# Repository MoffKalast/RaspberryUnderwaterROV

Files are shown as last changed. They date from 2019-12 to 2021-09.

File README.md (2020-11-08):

## Underwater ROV powered by a Raspberry Pi



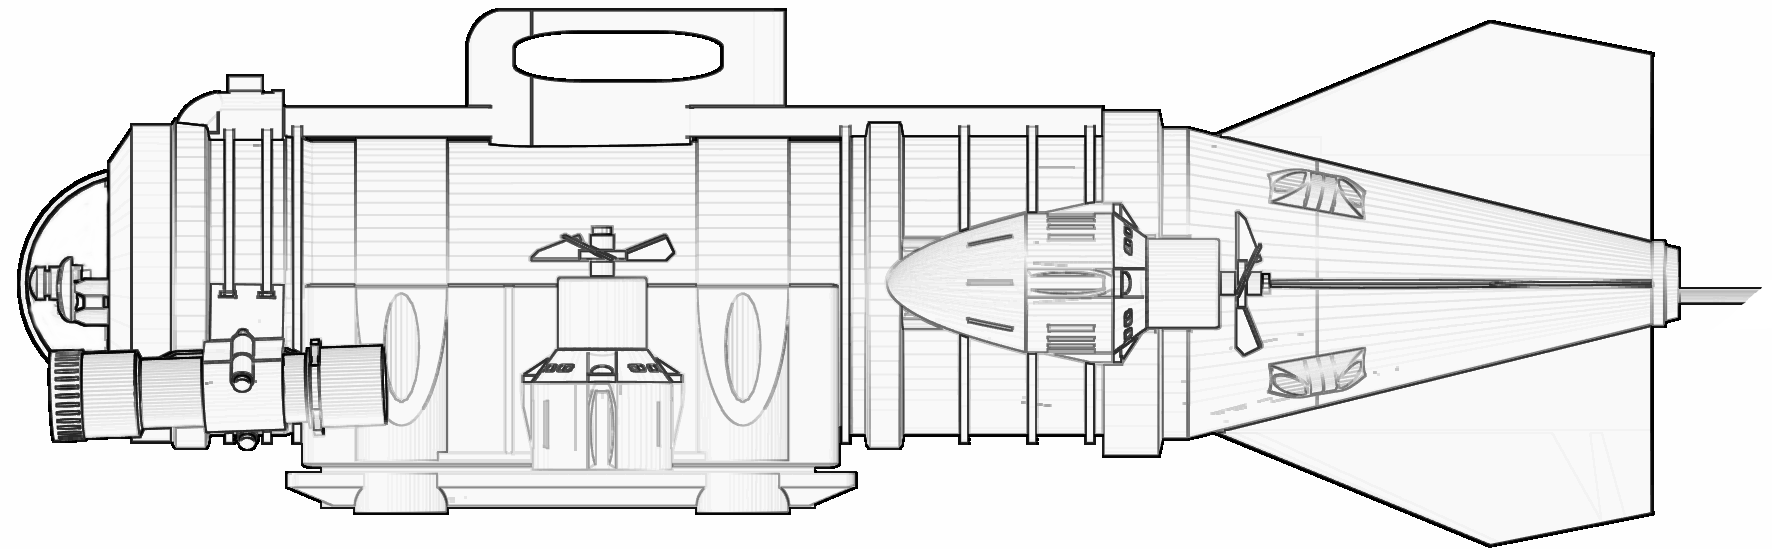
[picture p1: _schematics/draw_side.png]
Schematic


This codebase contains the control code for a homemade remotely controlled submarine and the Unity app for an android device that can be used to record video and drive the sub.

It uses a Raspberry Pi 2 as its central control unit, a Pi Camera V2 (later with D160 sensor) for custom video recording, sensors and drivers as described in the schematic below:

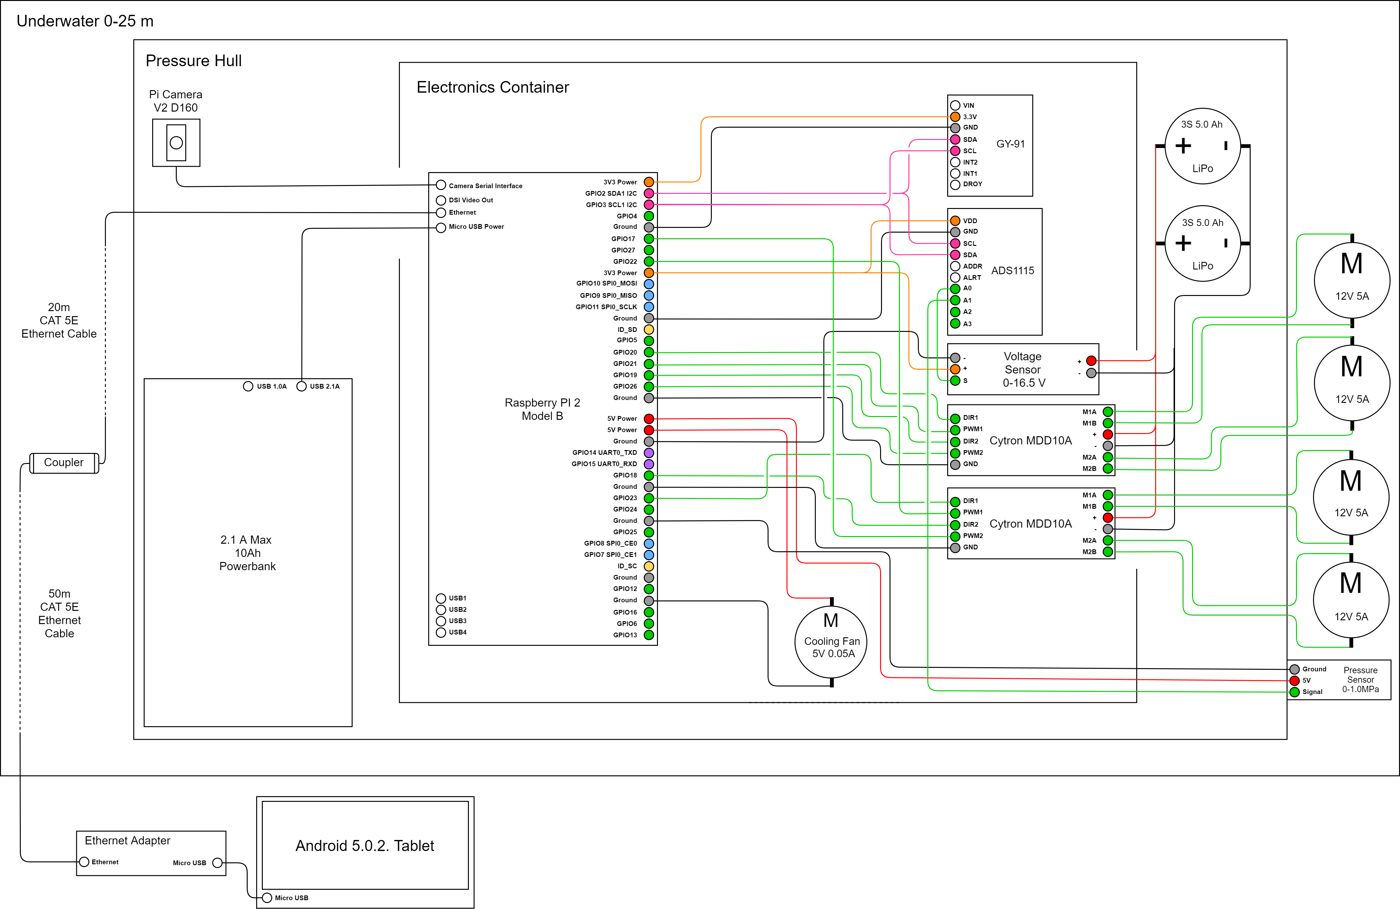
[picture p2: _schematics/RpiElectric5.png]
Electronics


The repository is divided into three parts:

- **/Submarine** which contains a NodeJS implementation of the submarine control software, along with video streaming and sensor AHRS, interfacting with the app using Socket.io

- **/ROVCommander** which is a Unity mobile app that allows for ease of control from a beach or boat

- **/ROViz** that contains the telemetry visualization application written in Godot (project source + exported Win64 binary)

See the subfolder README files for more information on each.

-------------

### Physical Implementation and Vehicle Tests

A test vehicle was constructed out of PVC-U sewer pipe with custom 3D printed PLA parts and an acrylic dome, all sealed together using epoxy glue.

Electronics

The following video contains a short summary of construction and testing.

IMAGE ALT TEXT HERE (https://www.youtube.com/watch?v=DufHhX7p4Xk)

All recorded uncompressed video during testing will be available for download if I ever find a place to host 50GB for free.

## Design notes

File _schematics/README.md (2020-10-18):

## Schematics

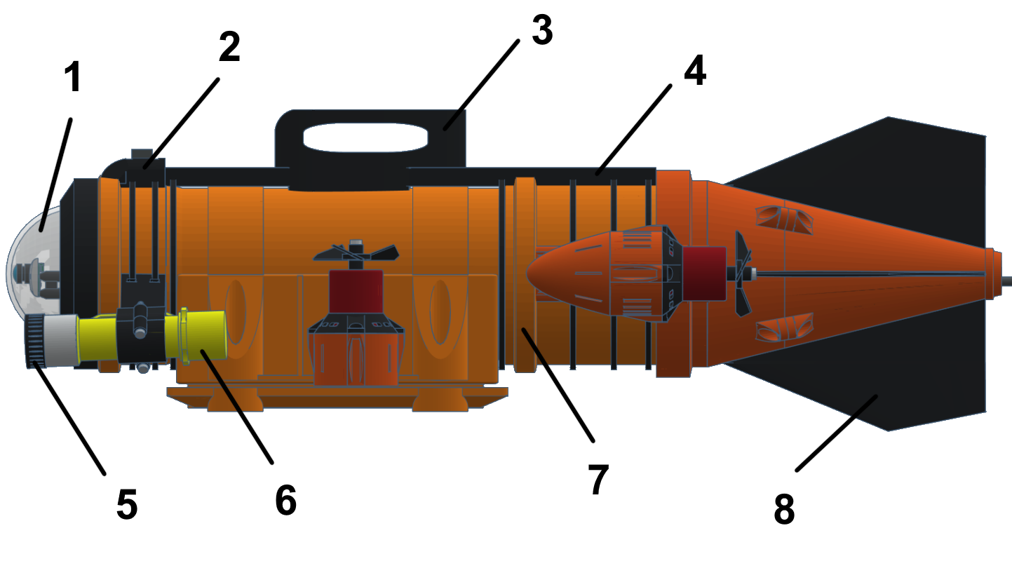
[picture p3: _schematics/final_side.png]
Schematic


1. Acrylic dome, 3mm thickness

2. GoPro mount

3. Sail/handle for stabilization and carrying

4. Sail rail

5. Light diffuser

6. Diving LED torches

7. Pressure hull (PVC sewer pipe)

8. Rear wings

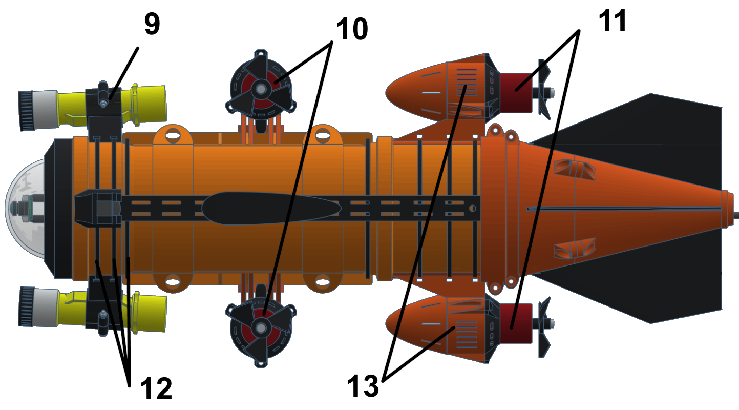
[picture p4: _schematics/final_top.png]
Schematic


9. Torch mount

10. Depth control thrusters

11. Planar motion thrusters

12. Zip ties

13. Engine nacelles

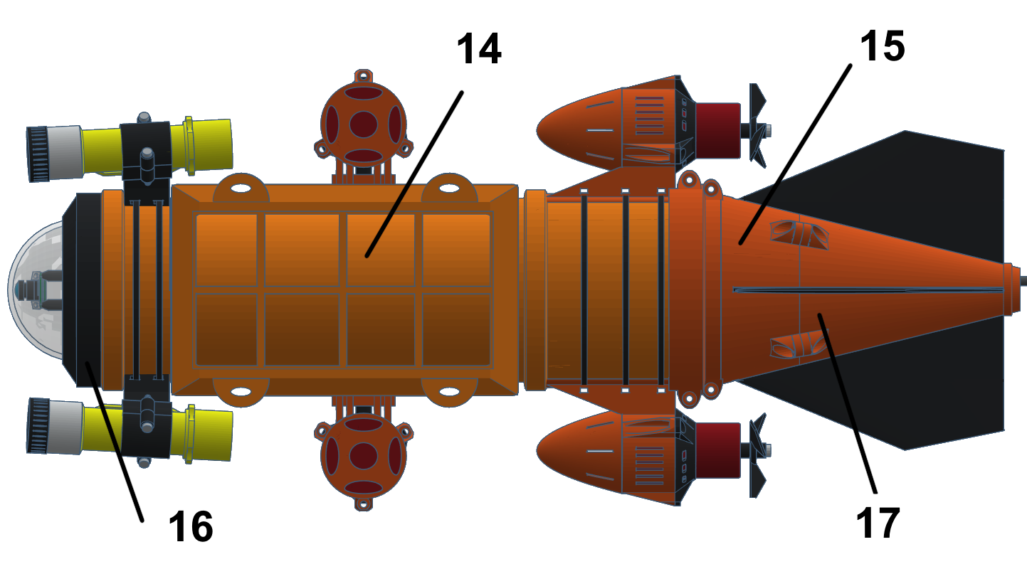
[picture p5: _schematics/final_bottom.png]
Schematic


14. Access hatch

15. Fixed tail assembly

16. Front shield

17. Detachable tail assembly

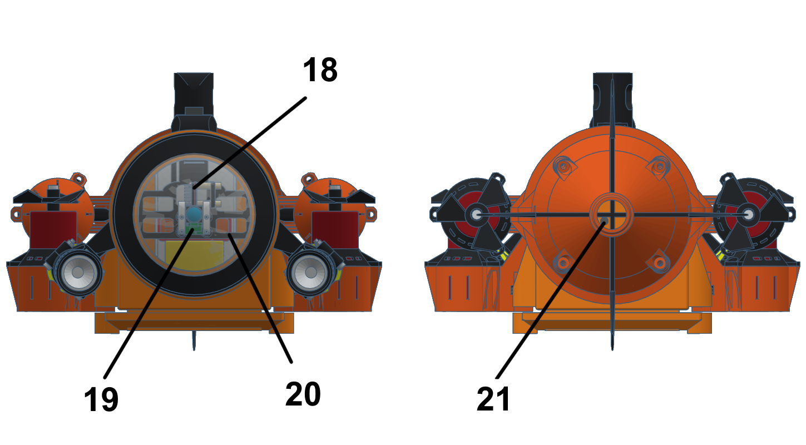
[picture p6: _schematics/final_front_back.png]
Schematic


18. IMU

19. Internal camera

20. IMU/camera mount

21. UTP cable

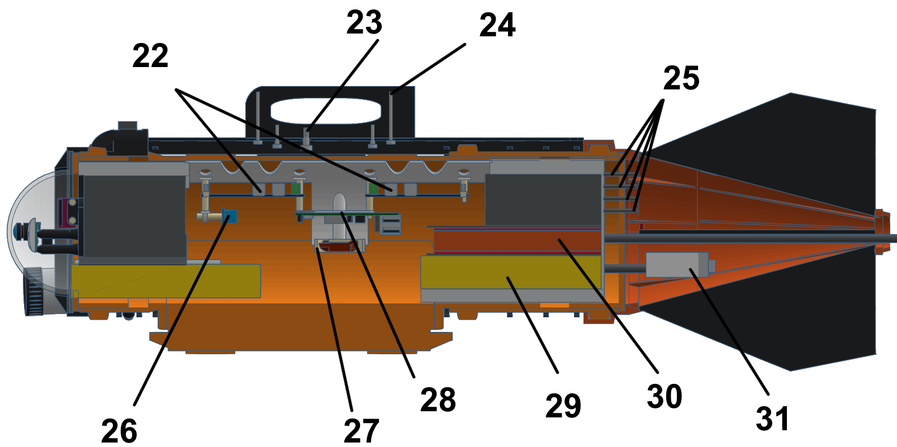
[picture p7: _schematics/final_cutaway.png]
Schematic


22. Motor drivers

23. M5 screw

24. M3 screw

25. Sealed motor wires

26. Voltage divider and ADC

27. 5V Fan

28. Raspberry Pi 2B

29. 5Ah 3S LiPo battery (motor supply)

30. 10Ah powerbank (Pi supply)

31. Water pressure sensor

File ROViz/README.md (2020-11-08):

### ROV Telemetry Visualizer - ROViz

A sort of RViz analogue app that visualizes recorded telemetry data in a 3D space using Godot 3.2.3.

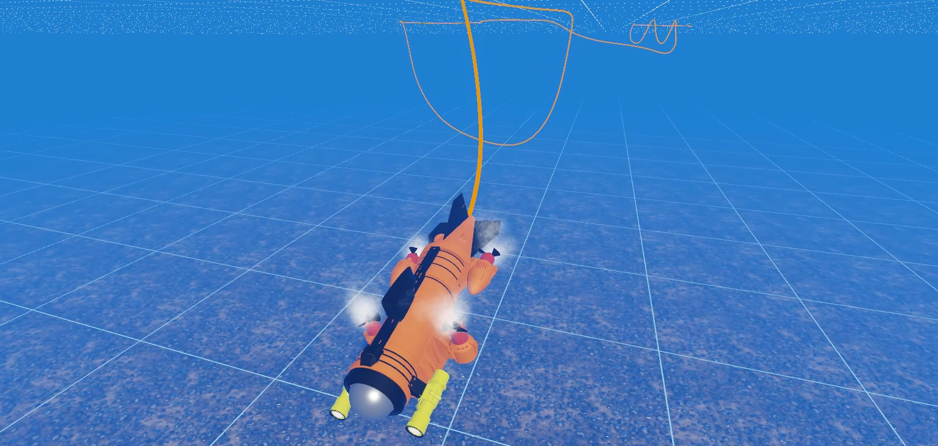
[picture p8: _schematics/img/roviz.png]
App


Features:
- 3D rendering of the submarine model with spinning propellers and particle effects
- raw value write out of currently displayed data
- timeline to track the data and a mark when the maximum depth was reached (after noise removal)
- file dialog to load telemetry files
- trail rendering to help track past movements

A curated collection of telemetry examples files can be found in the folder named as such.

Plugins used:

- [Godot-Trail-System](https://github.com/OBKF/Godot-Trail-System)
- [godot-realistic-water](https://github.com/godot-extended-libraries/godot-realistic-water/tree/master/realistic_water_shader)

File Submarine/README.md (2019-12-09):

## ROV Control Server

A NodejS implementation of a vehicle control software, mostly created to test out the absurd amount of Raspberry Pi hardware libraries for node on npm.

It enables differential drive control for two forward oriented thrusters, automatic heading and roll correction based on gyrocope data,  and depth hold based on pressure data and video streaming / recording using the Camera Module V2. Battery level is also approximated from voltage levels and battery type and forwarded to the control app along with internal hull air pressure, CPU temperature and air temperature.

When video recording is enabled a separate syncronized file of sensor data is also recorded and saved for later analysis.

Hardware Requirements:

- Raspberry Pi 2 B or later

- GY-91

- ADS1115

Software Requirements:

- Python 3

- NodeJS

- pigpio

Libraries used (all of these can be found by their name on NPM):

- data-store (storing settings, as all user inputed settings from the app are stored locally on the server, enabling quick switching of client devices in case one falls into water and dies)

- fs (sensor telemetry file writing)

- shelljs (enabling the app to run bash terminal commands on demand)

- python-shell (the node server runs a python script for video streaming since that seemed the only straightforward way to use the native python Raspicam library that enables usage of splitter ports)

- express, http, socket.io (communcation)

- pigpio (motor control)

- node-ads1x15 (reading the ADS1115 ADC for outside water pressure and battery level data)

- i2c (used for reading a LSM303 sensor that was later replaced by a GY-91)

- mpu9250 (9-dof sensor data readouts)

- bmp280-sensor (temperature and pressure readouts)

- ahrs (sensor fusion for 9-dof gyro/accelerometer/magnetometer sensor via a Mahony filter)

The modules are compiled for use on Raspbian Stretch and Raspberry Pi 2.

### Video Recording & Streaming

The software leverages the use of Raspicam splitter ports, allowing it to simultaneously stream/record video and save photos at different resolutions and formats.

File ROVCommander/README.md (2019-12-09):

### ROV Commander Unity App

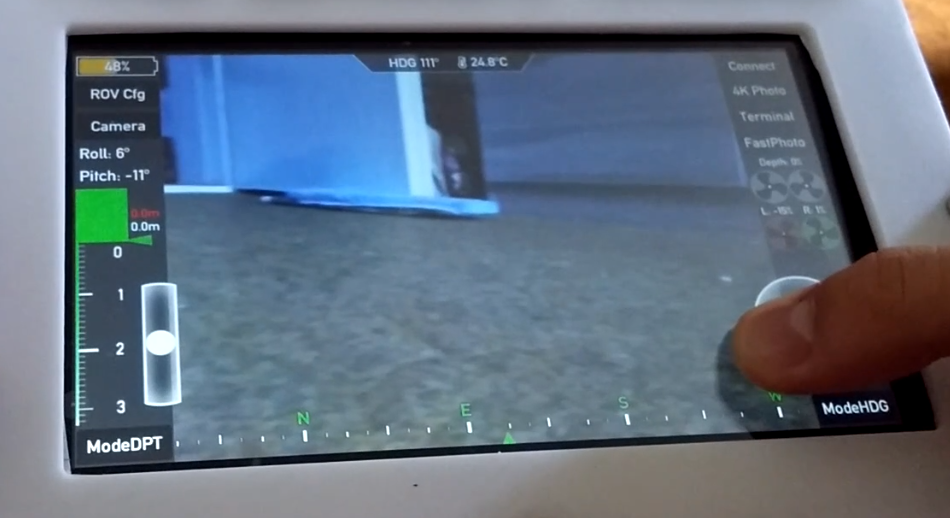
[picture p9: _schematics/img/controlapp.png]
App


Libraries used:

- [socket.io-unity](https://github.com/floatinghotpot/socket.io-unity)

- MjpegProcessor

The Unity project requires Unity 2017.4.26f1 due to the Socket.io library used for communication. The app presumes a LAN connection with the submarine control server, be it via an ethernet link + USB OTG or a wifi connection.

The app was developed exclusively for the Lenovo Tab 3, so minor gui tweaks may be needed for use on other devices.

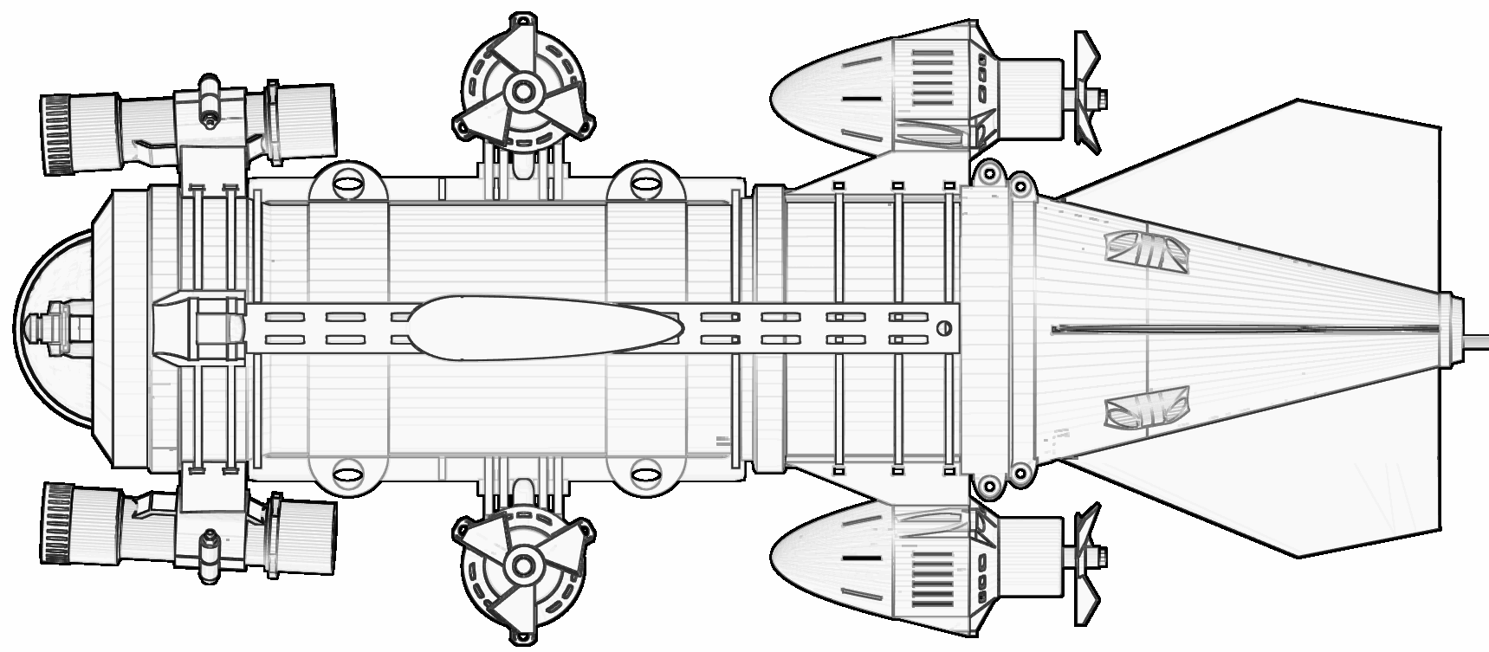
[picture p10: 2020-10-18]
_schematics/draw_top.png

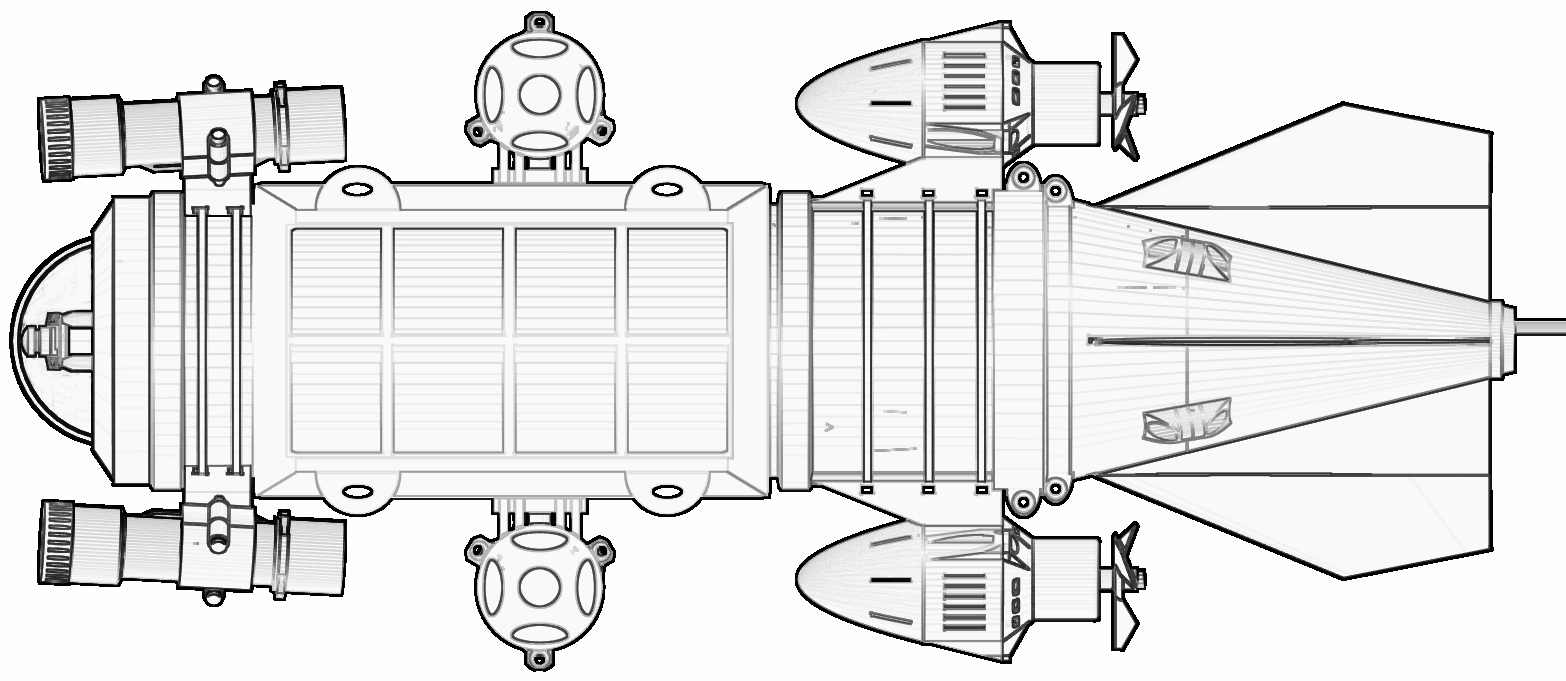
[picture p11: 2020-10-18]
_schematics/draw_bottom.png

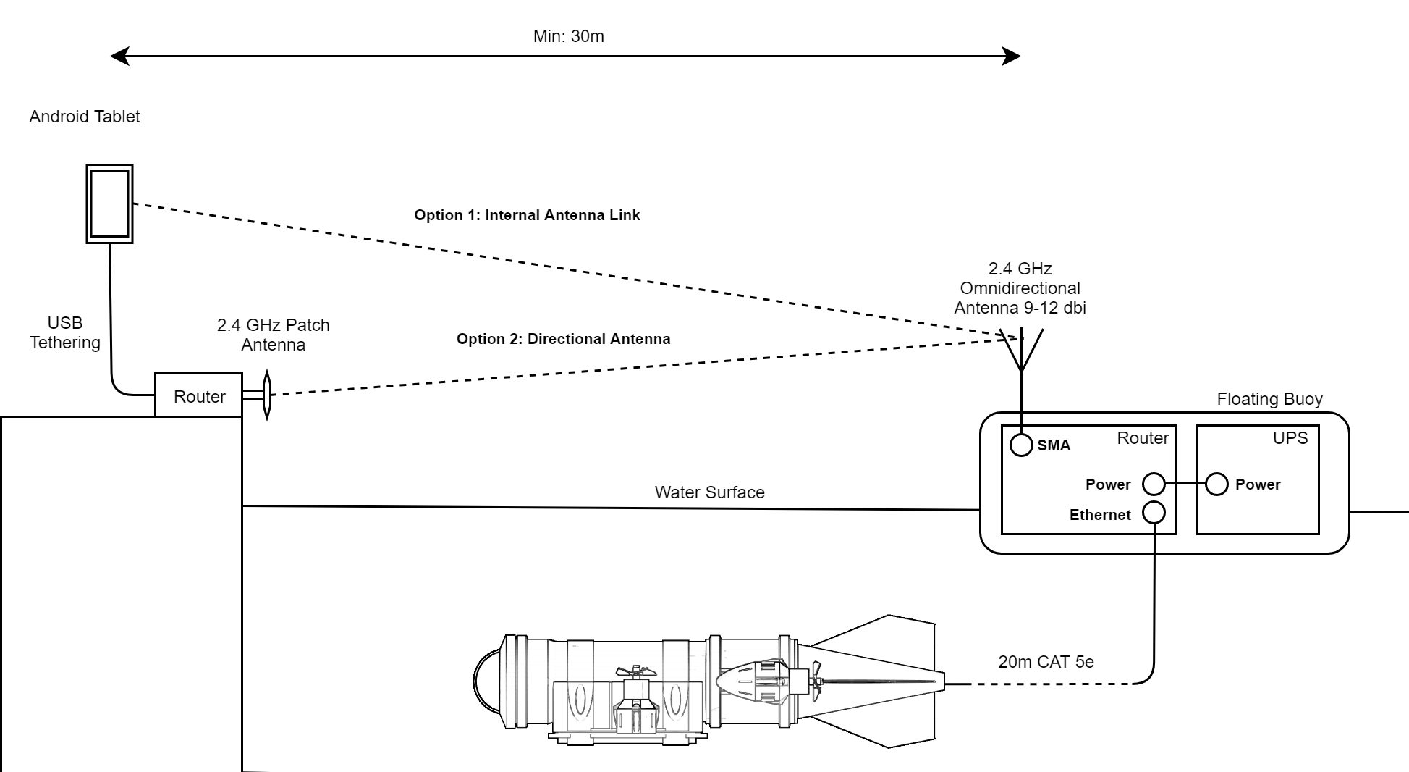
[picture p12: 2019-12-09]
_schematics/Link2.png

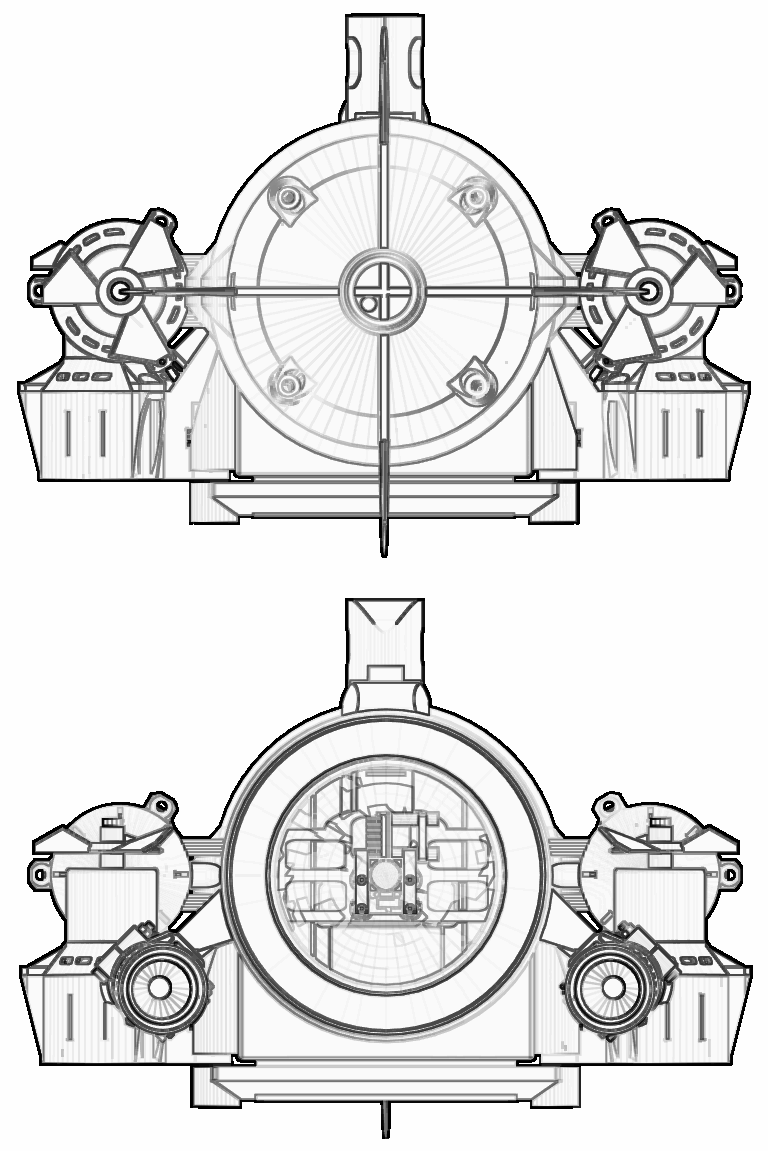
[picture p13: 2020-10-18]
_schematics/draw_front_back.png

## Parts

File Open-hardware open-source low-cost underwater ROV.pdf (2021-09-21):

# Open-hardware open-source low-cost underwater ROV

Vid Rijavec, Danijel Skocaj ˇ

University of Ljubljana, Faculty of Computer and Information Science E-mail: vid.rijavec@gmail.com, danijel.skocaj@fri.uni-lj.si

Abstract

As monitoring coastal regions becomes ever more topical due to unforeseen changes in ecosystems there still has not been a major breakthrough in marine robotics when it comes to mass accessibility. In this work we present our low-cost prototype of an underwater remotely operated vehicle (ROV) for coastal exploration and monitoring. We present the mechanical, electrical and software components of the developed ROV and describe the results of field tests. We made all the data, schematics, software, and documentation needed for construction of a such low-cost vessel publicly available.

Keywords

ROV, submarine, low-cost, Raspberry Pi

### 1 Introduction

Robotics has been making major strides in worldwide adoption, especially in unmanned ground and aerial vehicles (UGVs and UAVs) where prices have been dropping and with household robots entering mass production. The same cannot be said regarding autonomous underwater vehicles (AUVs) and remotely operated underwater vehicles (ROVs). The potential for such vessels includes controlling and monitoring large underwater areas without a large crew of divers and by users without diving certification. A number of species are already on the decline due to climate change [1], and those are being replaced by others, affecting ecosystems in unpredictable ways. As such, having access to more effective and low-cost AUVs and ROVs could help in detecting changes sooner, allowing for faster response and potential food chain collapse prevention. Similar applications involving monitoring coastal regions by utilising such an underwater robot are numerous.
There are many commercial options for buying a research ROV. High-end versions include the iBubble EVO [2] or the Blue Robotics BlueROV2 [3], with projects like the Blue Dot Model C [4] presenting a more affordable but less capable option. Given that even the low-cost options still aren’t truly affordable most enthusiasts still prefer to construct their own do-it-yourself (DIY) research vessel to customize it to their needs. However, most of these attempts tend to still be bulky and analog.

Our vessel, shown in Fig. 1, is designed as a combination of the classical AUV torpedo-like design and the typical boxy ROV designed for high movement accuracy, by combining the hydrodynamic hull shape with multiple control thrusters to allow for more degrees of freedom than a singular rear propeller. Our intention was to construct a fast-moving ROV that can explore a coastline from shore, one that’s controlled by a pilot using a tablet computer but offers advanced stabilization functions and an autopilot for ease of use. As such our design is a compromise between the two underwater vehicle types, giving the vessel greater speed at the cost of some maneuverability.

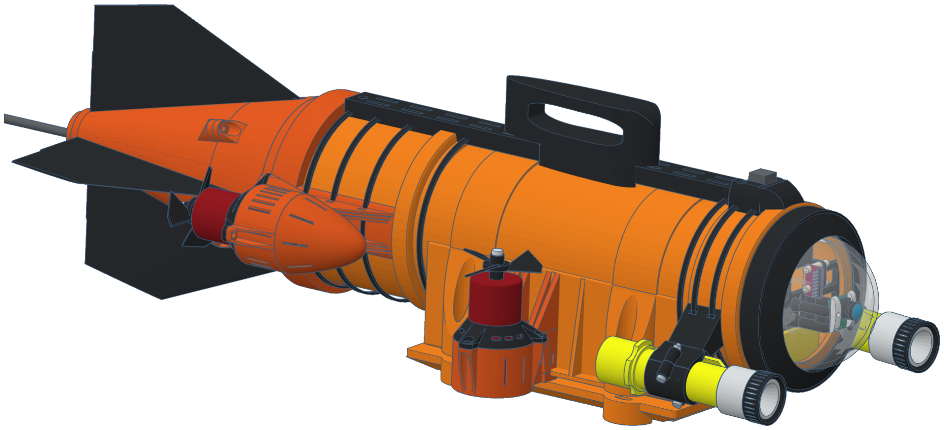
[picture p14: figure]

Figure 1: ROV CAD Model. The visible components of the vessel are: a PVC pressure hull, external LED lights, modified bilge pump thrusters (allowing movement in 4-DoF), rear stabilizers, a top handle, and a transparent camera dome.

The paper outlines the system and the specific components we’ve developed for it, with the rest of the code, schematics and documentation being available on Github [5].

### 2 Mechanical design

Figures 2, 3 and 4 present an overview of the ROV and its component parts, along with the tablet computer used by the pilot. The entire vessel is approximately 74 cm long and weighs just over 10 kg with batteries.
Building a sturdy and resistant pressure hull requires a rigid and non-permeable material that can be effectively glued to other parts. Out of all the tested low-cost components, the most cost-effective parts were determined to be PVC-U sewer pipe sections. We’ve used a cleaning section of pipe to make up the majority of the hull, as it has an external hatch which is practical for accessing internal electronics.
The front of the vessel is capped with an acrylic dome with a thickness of 3 mm, to allow the internal camera to see the underwater environment. It’s attached to the sewer pipe hull using epoxy glue and silicone caulking. The curvature of the dome later proved to be detrimental to the video quality as it added unwanted distortions and reflections. A more optimal design would involve the use of a thicker but flat (but smaller) front window. The video is then processed and sent over a length of rugged CAT 5E cable.

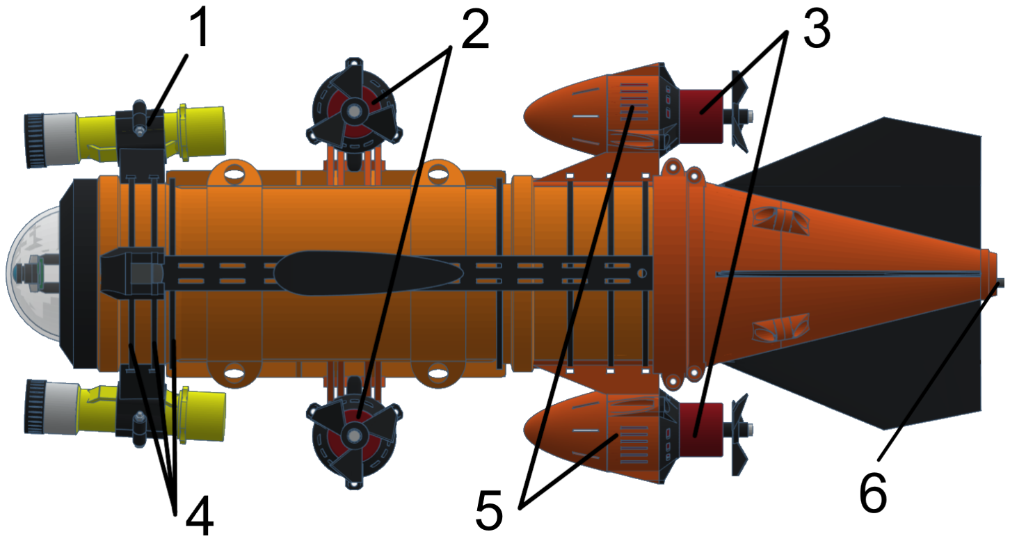
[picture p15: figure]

Figure 2: Top view of the vessel. 1. PLA flashlight mount. 2. Depth control thrusters. 3. Horizontal movement thrusters. 4. Zip ties. 5. PLA thruster nacelles. 6. CAT 5E cable.

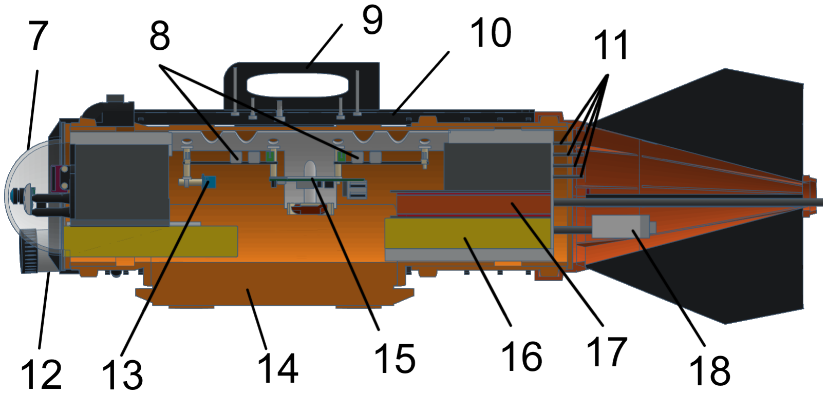
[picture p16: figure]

Figure 3: Internal cutaway of the vessel. 7. Transparent dome containing the Pi camera and IMU. 8. Cytron MDD10A motor drivers. 9. Dual purpose top fin and handle. 10. Steel structural rail. 11. Motor wires. 12. Diving flashlights with diffusers. 13. Voltage divider and ADC. 14. Access hatch. 15. Single board computer. 16. 2x 5 Ah 3S LiPo batteries. 17. 5 V 10 Ah Power bank. 18. Water pressure sensor.

Submersible DC bilge pump motors intended for clearing out any water that seeps into a ship’s bilge are a common choice for DIY ROV construction. The main appeals are the low cost, ease of modification and full water ingress protection. A simple improvement is to remove the pump’s impeller and housing, replacing them with a more efficient propeller [6] to achieve higher (and reversible) thrust. Our prototype uses nylon boat propellers sized at 56 mm. These motors do have a drawback -the o-ring seal around the shaft which exerts increasing amounts of drag with increasing pressure [7]. The seals fully block the shaft from rotating at around 25 m, which limits the sub’s operational depth. As such, using fully flooded brushless motors may be a better fit if greater depths are needed.
Rear wings aid with stabilization when moving at speed and were also chosen to be constructed out of PVC due to its light weight. The tail itself is not pressurized (typically called an outer or light hull which allows for water ingress) and houses the water pressure sensor, the tail fins, and protects the power/data cables along with providing better hydrodynamic performance.

### 3 Hardware and electronics

The electronics system as seen on the cutaway in Fig. 3 is centered around a single board computer, specifically the Raspberry Pi 2 Model B+, due to its low cost and lower TDP than later versions. The key features were GPIO pin access and the RJ45 socket which allows for an Ethernet link between the vessel and the control app on the surface. The surface component is a low-cost Lenovo tablet computer encased in a 3D printed housing that connects to the Ethernet link using an external USB dongle as seen in Fig. 4.

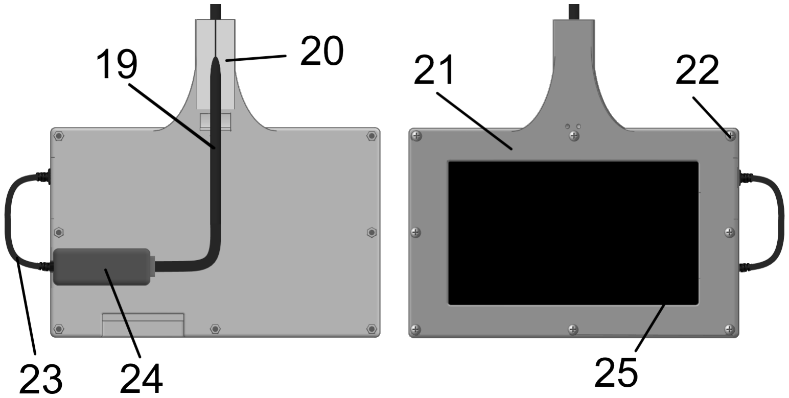
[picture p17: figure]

Figure 4: Tablet-based remote control system. 19. Reinforced CAT 5E cable (70 m total). 20. Cable clamp. 21. 3D printed splash-proof housing. 22. M3 screws. 23. Micro USB connector. 24. Ethernet network card. 25. Lenovo Tab 3.

### 3.1 Propulsion

As the ROV uses DC brushed motors (with a current rating of 5 A), we chose low cost Cyron MDD10A motor drivers to connect them to the Pi. Since the current rating of the drivers is twice the required maximum we can count on lower internal heating.

### 3.2 Sensors

The ROV is equipped with various sensors: an IMU, a water pressure (depth) sensor, a battery voltage sensor, an internal air pressure and a temperature sensor. We’ve also used a Pi Camera Module v2, and later the D160 fish eye modification for video recording.
We’ve used the MPU9250 IMU, which offers an accelerometer, gyroscope and magnetometer. The expansion board used is the GY-91 which also contains a BMP-280 pressure and temperature sensor, so that is used to log the state of internal air as well.
For the water pressure sensor we’ve selected a low-cost transducer intended for measuring the pressure inside hoses with a capability of 0.8 MPa (which equates to roughly 80 m depth of seawater). As the sensor is analog and the Pi has no analog reading pins we’ve also added a 10 bit 4-channel ADC to link the two together. As the ADC has spare channels we can also measure battery level using a voltage divider circuit.

### 4 Software

We’ve based our software around a socket.io link, which allows communication between the C# Unity app running on the remote control tablet, and the node.js server running on the submarine itself, which controls most of the functionality. To avoid having a rooted system on the tablet and a static IP, the Raspberry Pi instead acts as a DHCP server and assigns a known IP to any Ethernet connected device.
Not all of the system can be managed with node.js directly, as the libraries that allow full Pi Camera configuration have only been provided for Python and C++. Since the system requires the usage of GPU splitter ports to simultaneously stream and record video while taking pictures, the camera control part ended up being implemented in Python, which is then launched and managed from the node.js server.

### 4.1 Stabilization

We implemented two automatic functions: depth hold and heading hold. Establishing proportional control between the detected depth and target depth turned out to be enough to archive a satisfactory depth hold.
A more advanced system was required for holding a specific heading. An AHRS IMU fusion system [8] was added to get a good internal belief state regarding the submarine’s orientation. We’ve then implemented a 360-degree-capable proportional rotational system, which allows the pilot to input a single forwards or backwards speed while the vessel holds orientation.
Full PID controllers did not turn out to be required for adequate stabilization due to high drag and inherent damping and were also infeasible to properly tune during operation.
The system manages the aforementioned sensors and streams their data to the tablet, uses them internally for stabilization and also records them into a log file for later use.

### 4.2 Remote control app

We’ve implemented a front-end interface for controlling and configuring the submarine from a tablet computer, which was developed using Unity. The video arriving from the camera in a mjpeg format is displayed using an adapted version of the Mjpegprocessor library [9], while the rest of the telemetry and commands get routed through the socket.io library [10]. Fig. 5 shows the GUI while streaming the image of a calibration board, which indicates the camera field of view.
The main functionality is remote control, which is done either with manual joysticks or by selecting a direction using the bottom compass bar and a depth using a vertical depth indicator. In order to provide as much

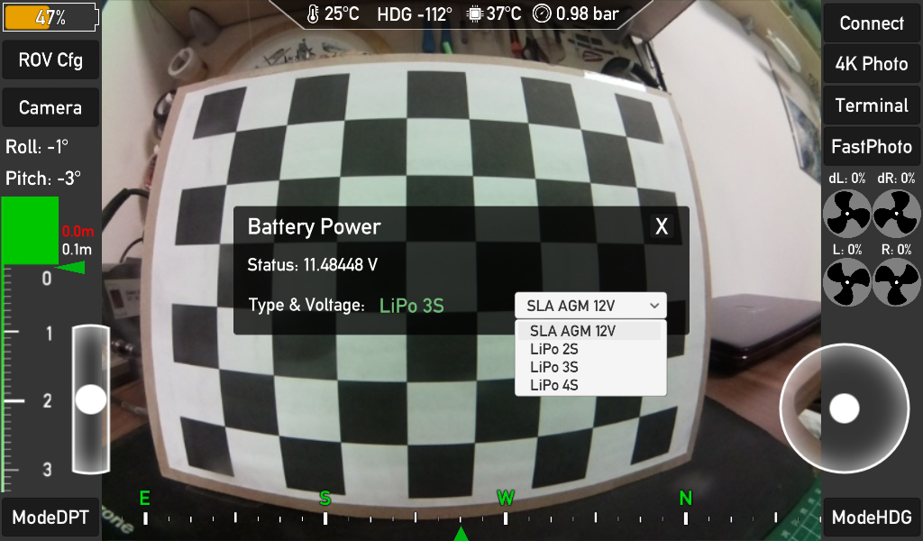
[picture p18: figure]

Figure 5: Layout of the tablet interface, showing the relevant telemetry and video feed.

on-site debugging power, the app can set all stabilization and video recording parameters and allow for rudimentary terminal access.

### 4.3 Visualization and analysis

We built a Godot engine visualizer to attempt to process the recorded log file data and reconstruct the ROV’s odometry to some degree as seen in Fig. 6.
The logged data gives us two absolute measurements: rotation (based on the fused IMU data) and depth (calculated from water pressure readings). It’s not possible to completely determine the movement path using just these two values, however, we also logged the individual thrusters’ speeds which were used to infer movement velocity. While it’s not possible to compensate for drift due to waves and currents the resulting movement path is still good enough in most cases.
While the data was logged every 100 ms, the visualization ran at a higher frequency (16 ms for 60 frames per second) so the data had to be linearly interpolated for smooth movement. A synced on-board video of a dive with the telemetry visualization which can be viewed on Youtube [11].

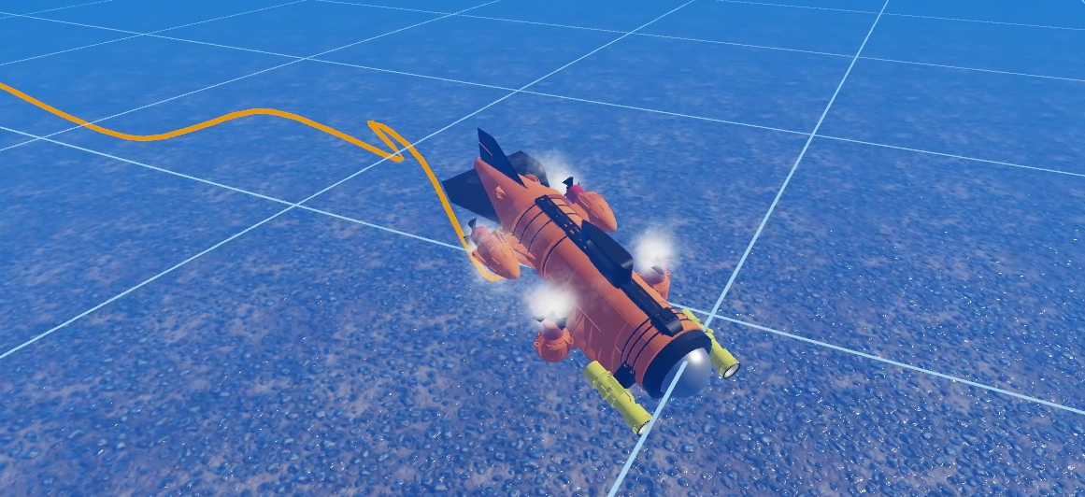
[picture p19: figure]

Figure 6: The ROV being rendered in Godot, visualizing a recorded dive and drawing a trail behind the vessel.

### 5 Evaluation and testing

The finalized ROV shown in Fig. 7 performed as required and is capable of exploring a coastal area while recording clear video as shown in Fig. 8. An edited compilation of video recordings that sums up research, construction and testing can be viewed on Youtube [12].

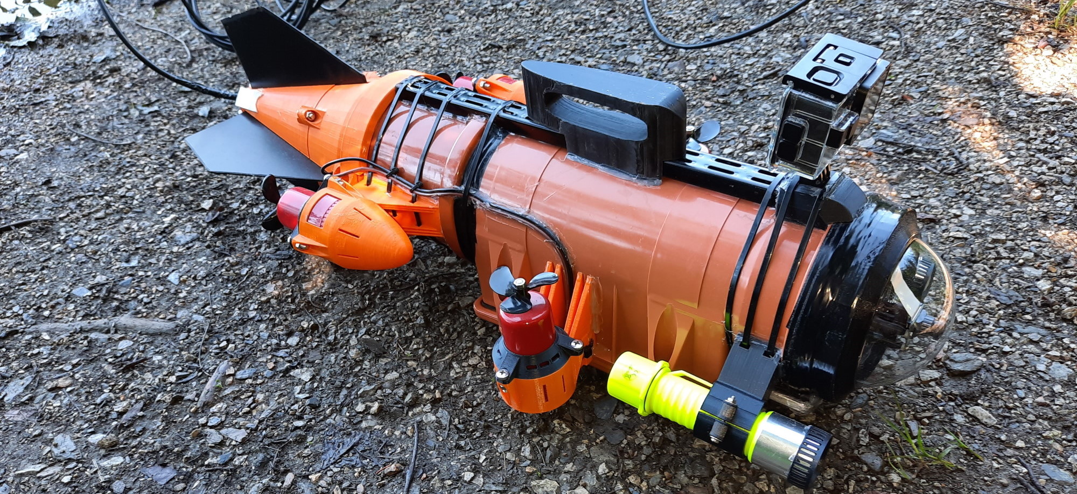
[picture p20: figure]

Figure 7: The ROV with an action camera mounted on the top rail.

To determine the effects of different buoyancy on the system’s operation, tests were done in both salt and fresh water. The difference ended up being minor, however, the depth calculation can be off by 2.5 % due to the extra mass of salt water. We therefore added parameters that can be changed in the mobile app to compensate for the changing environment.
We’ve used two different action cameras to record external video during testing: the Apeman A80 and later a GoPro Hero 9 Black combined with a red filter as the previous setup proved unsatisfactory. Having a red filter allows us to do an initial colour correction by restoring the lower wavelengths which get absorbed far more in water and lead to over-saturation of green and blue.
The recorded data shows that the air pressure in the ROV stays relatively constant regardless of depth, which would mean that there is minimal flex in the pressure hull as intended. The internal air temperature also stayed close to the external water temperature. It would appear the lack of isolation in the hull provides for excellent cooling and would allow for higher TDP computers to work without issues.

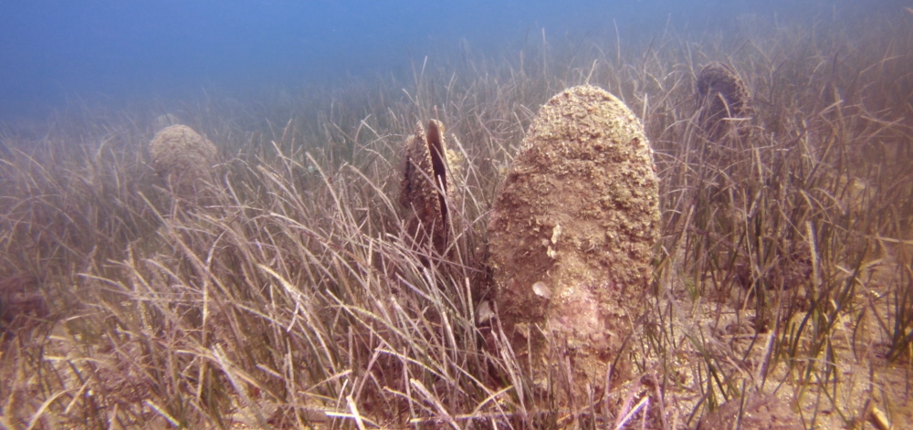
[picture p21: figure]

Figure 8: Fan mussles which were found in large numbers when testing in Izola, some of them decayed due to parasite infestation, confirming news sources [13].

Another addition to the system would be a sonar system for sea floor and obstacle detection, however, there are no affordable sensors that are capable of being integrated into a custom system at this time. One would need to construct a custom driver circuit for a commercial fish finder sonar transducer (e.g. TL88E, XF02), as conventional sonar sensors designed for AGV/AUV atmospheric usage lack the required power and do not operate in effective frequencies, which lowers the range and accuracy under water to unusable levels.

### 6 Conclusion

In this paper, we described the process of building a low-cost underwater DIY ROV with open-source hardware and software, useful for light research and monitoring of shallow coastal regions. We’ve achieved this goal by choosing a crush depth of 25 m and used less resistant and subsequently cheaper materials, as well as using 3D printed components to fill the gap between other parts. The total cost of the system ended up being around 400 C, excluding the tablet computer and action cameras.
The vessel is stable enough to record useful video due to the included IMU and sensor fusion, while being able to utilize its high top speed to rapidly traverse a chosen area and locate points of interest. The external mechanical design is robust enough to handle expected conditions, however the electrical internal setup could be further improved by designing a dedicated printed circuit board.

### 7 Acknowledgements

The authors would also like to thank professors Dr. Nikolaj Zimic and Dr. Matjaz Vidmar for their help and con- ˇ tributions in the research phase of the project.

References

[1] Marine Food Webs Are on the Brink of Collapse Because of Climate Change, https://futurism.com/marine-foodwebs-brink-collapse-because-climate-change
[2] iBubble - Your Personal Underwater Cameraman, http://ibubble.camera/product/ibubble-autonomousunderwater-drone
[3] Blue Robotics, http://bluerobotics.com
[4] Blue Dot Underwater Drones, https://www.bluedotrov.com
[5] Source code, schematics and documentation, https://github.com/MoffKalast/RaspberryUnderwaterROV
[6] Homebuilt ROVs - Seafox Retrofit Thrusters, https://www.homebuiltrovs.com/seafoxretrofitthrusters.html
[7] Homebuilt ROVs Mayfair 750 GPH Bilge Pump Thruster Testing,
http://www.homebuiltrovs.com/mayfair750test.html
[8] ahrs - npm, https://www.npmjs.com/package/ahrs
[9] SampleUnityMjpegViewer, https://github.com/DanielArnett/SampleUnityMjpegViewer
[10] socket.io-unity,
https://github.com/floatinghotpot/socket.io-unity
[11] ROViz visualization,
https://www.youtube.com/watch?v=M0sli2o5RJY
[12] Construction and testing video, https://www.youtube.com/watch?v=DufHhX7p4Xk
[13] Slovenian sea researchers uncover a number of deceased fan mussles, https://www.sta.si/2797119

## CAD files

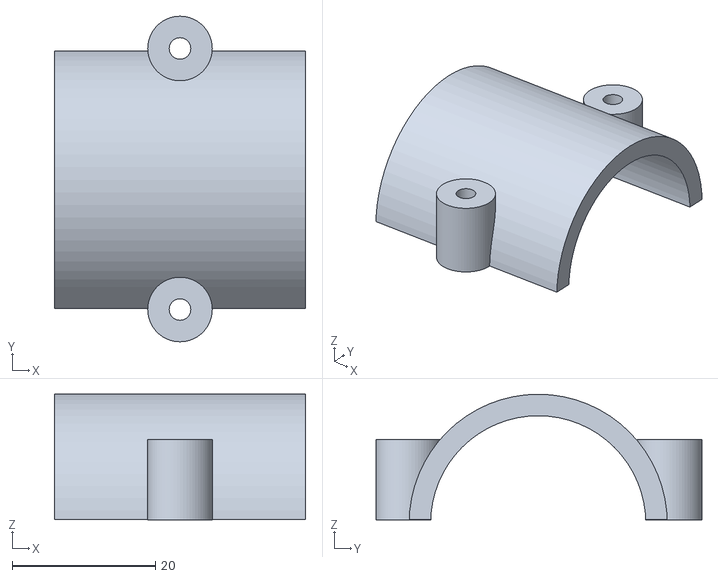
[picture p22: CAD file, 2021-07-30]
_schematics/cad/lamp_mount_clamp.stl
35.0 x 45.4 x 17.5

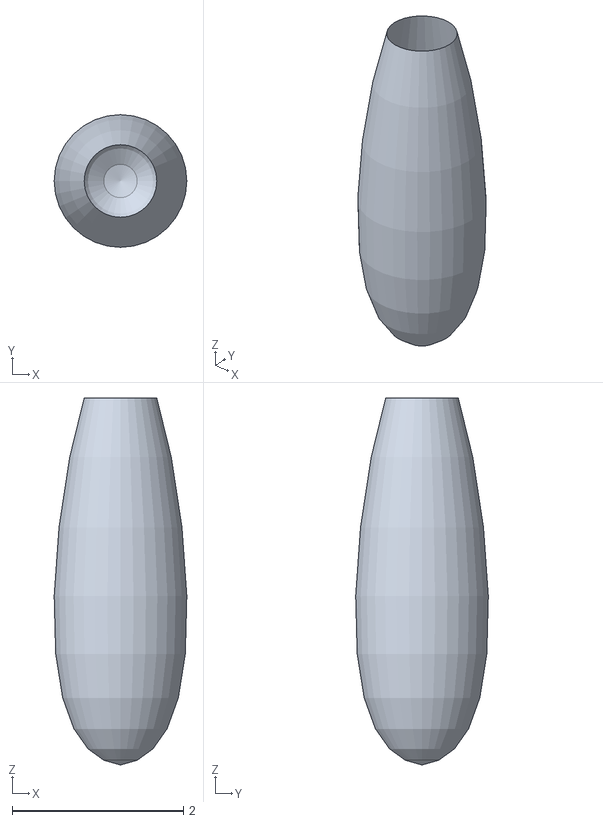
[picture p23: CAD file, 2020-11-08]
ROViz/source/assets/projectile_shape_1.obj
1.55 x 1.55 x 4.29

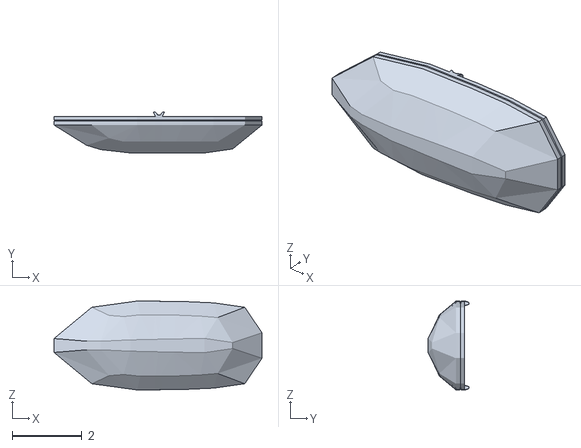
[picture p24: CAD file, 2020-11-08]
ROViz/source/realistic_water_shader/art/boat/Boat.obj
5.95 x 1.17 x 2.54

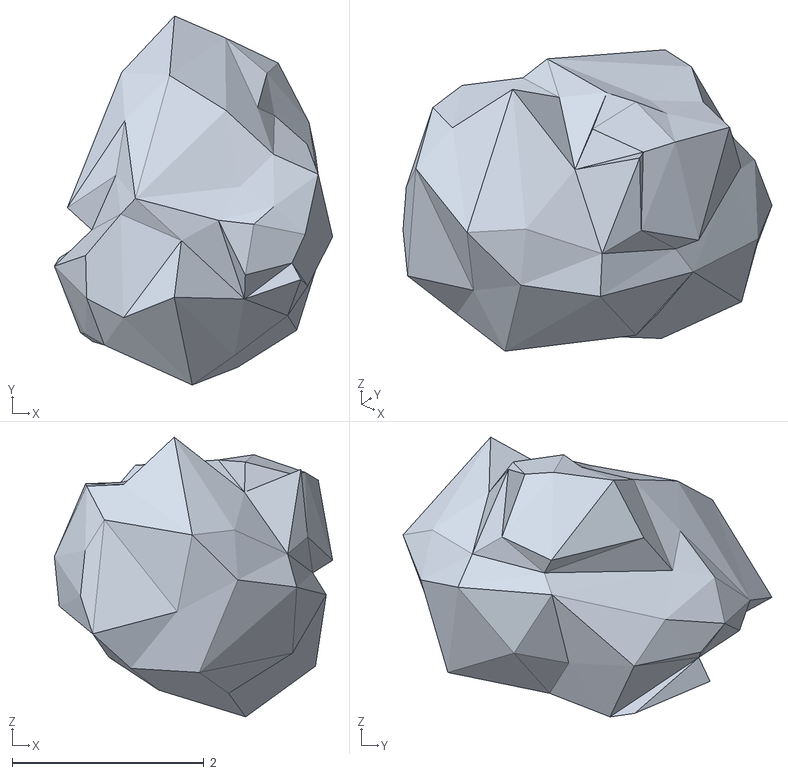
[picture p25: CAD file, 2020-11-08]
ROViz/source/realistic_water_shader/art/rock/Rock.obj
2.91 x 3.85 x 2.92

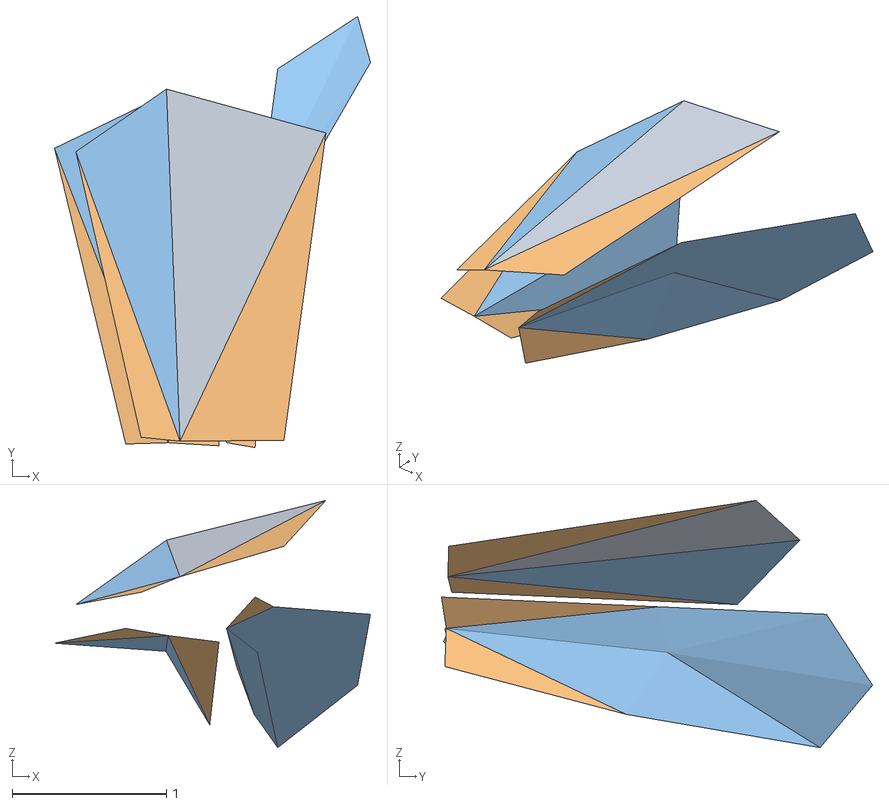
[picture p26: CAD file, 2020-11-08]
ROViz/source/realistic_water_shader/art/seaweed/Seaweed.obj
2.05 x 2.80 x 1.60
Seaweed_Seaweed_Seaweed
Ground
Wind

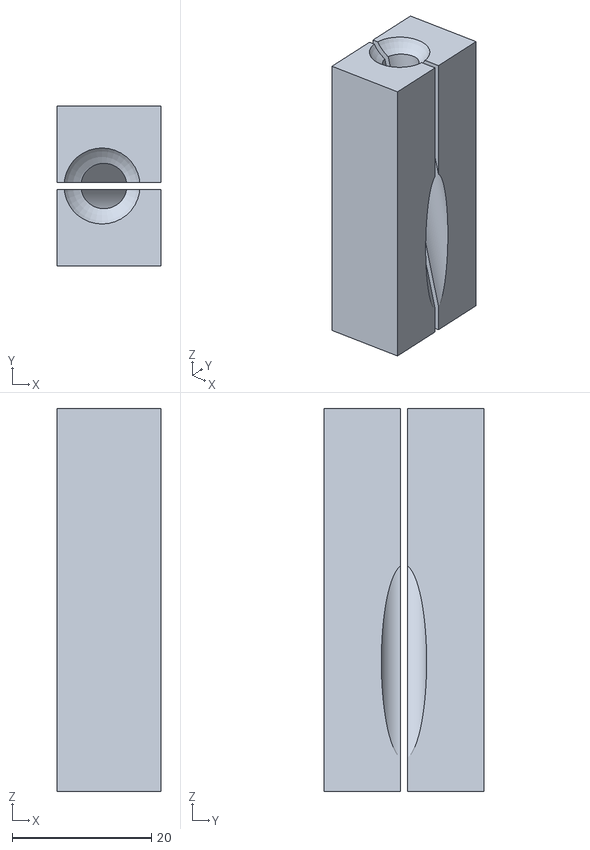
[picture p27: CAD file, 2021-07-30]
_schematics/cad/utp_crimp.stl
15.0 x 23.0 x 55.0

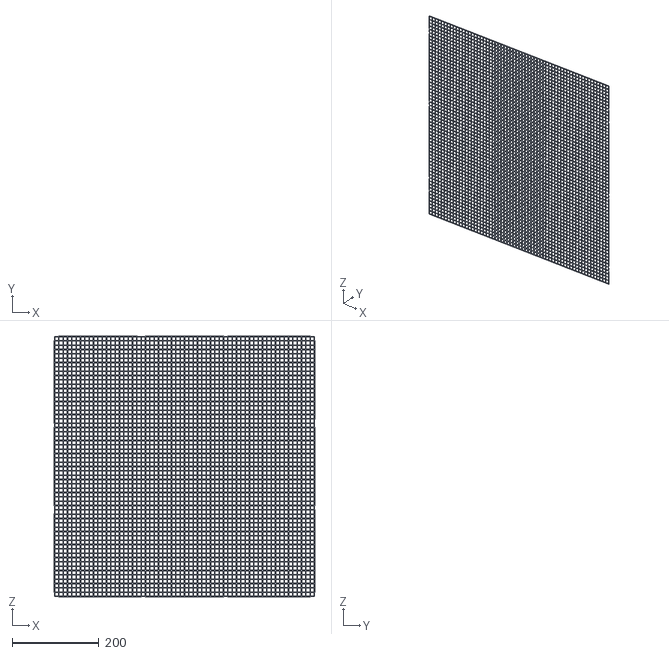
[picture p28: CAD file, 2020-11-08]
ROViz/source/assets/grid.obj
599.9 x 0 x 599.9

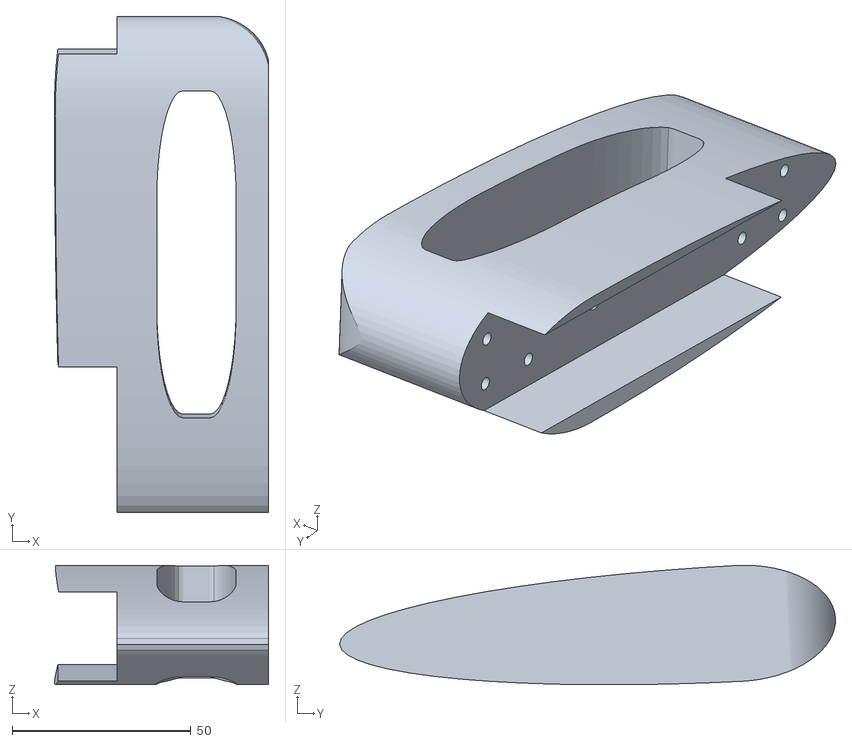
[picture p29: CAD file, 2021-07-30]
_schematics/cad/topsail.stl
60.0 x 138.9 x 33.5

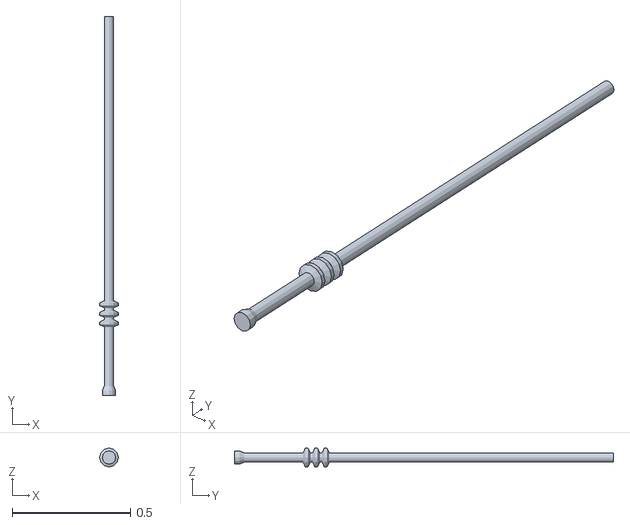
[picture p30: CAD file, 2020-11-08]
ROViz/source/assets/sword.obj
0.08 x 1.60 x 0.08

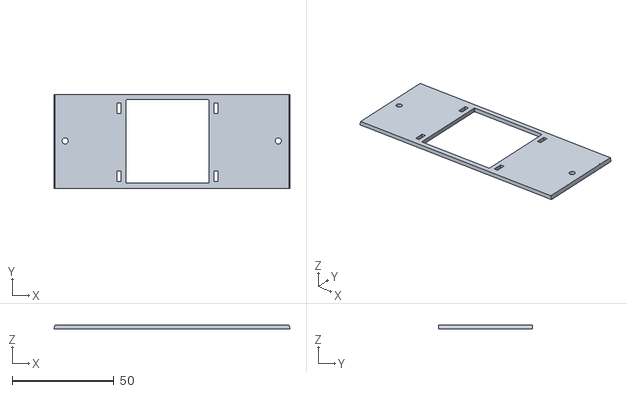
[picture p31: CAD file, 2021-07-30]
_schematics/cad/electronics_mount_fanplate.stl
116.0 x 46.1 x 2.00

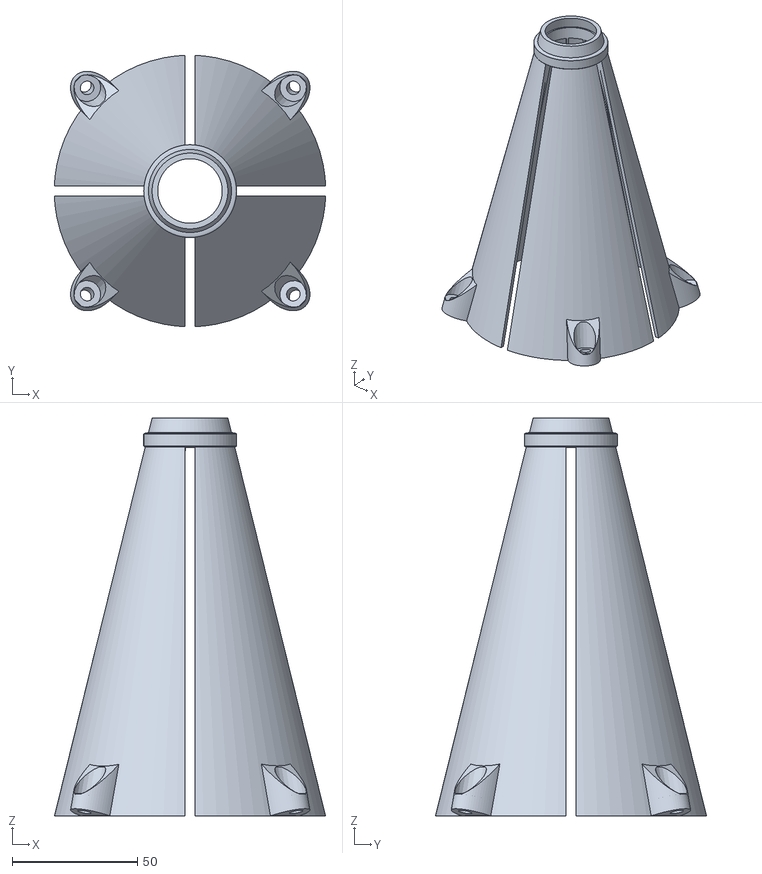
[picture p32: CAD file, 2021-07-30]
_schematics/cad/rear_cone_1.stl
108.1 x 108.1 x 158.6

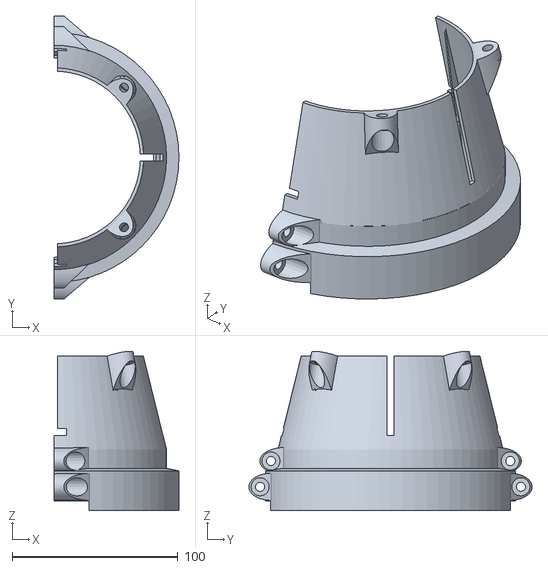
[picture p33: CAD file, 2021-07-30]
_schematics/cad/rear_cone_2.stl
75.5 x 171.0 x 96.4

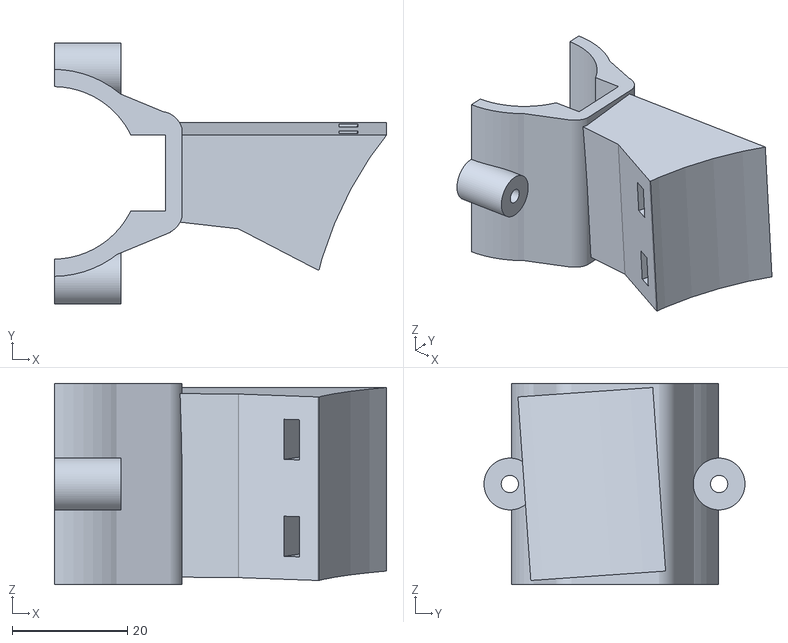
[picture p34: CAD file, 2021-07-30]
_schematics/cad/lamp_mount_starboard.stl
57.7 x 45.4 x 35.0

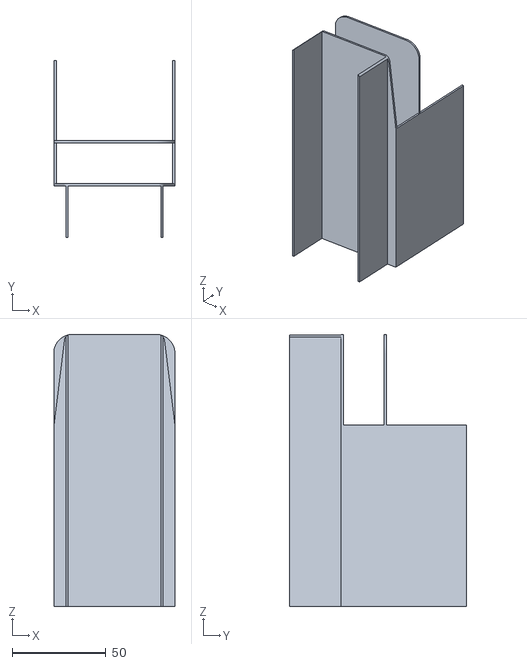
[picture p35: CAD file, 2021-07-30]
_schematics/cad/battery_compartment_rear.stl
64.6 x 94.7 x 145.4

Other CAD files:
_schematics/cad/rear_cone_3.stl
_schematics/cad/nacelle_vertical.stl
_schematics/cad/rear_wing_clamp.stl
_schematics/cad/sensors_mount.stl
_schematics/cad/actioncam_mount.stl
_schematics/cad/battery_compartment_front.stl
_schematics/cad/dome_shield.stl
_schematics/cad/electronics_mount_1.stl
_schematics/cad/electronics_mount_2.stl
_schematics/cad/lamp_diffuser.stl
_schematics/cad/lamp_mount_port.stl
_schematics/cad/nacelle_cover.stl
_schematics/cad/nacelle_horizontal.stl

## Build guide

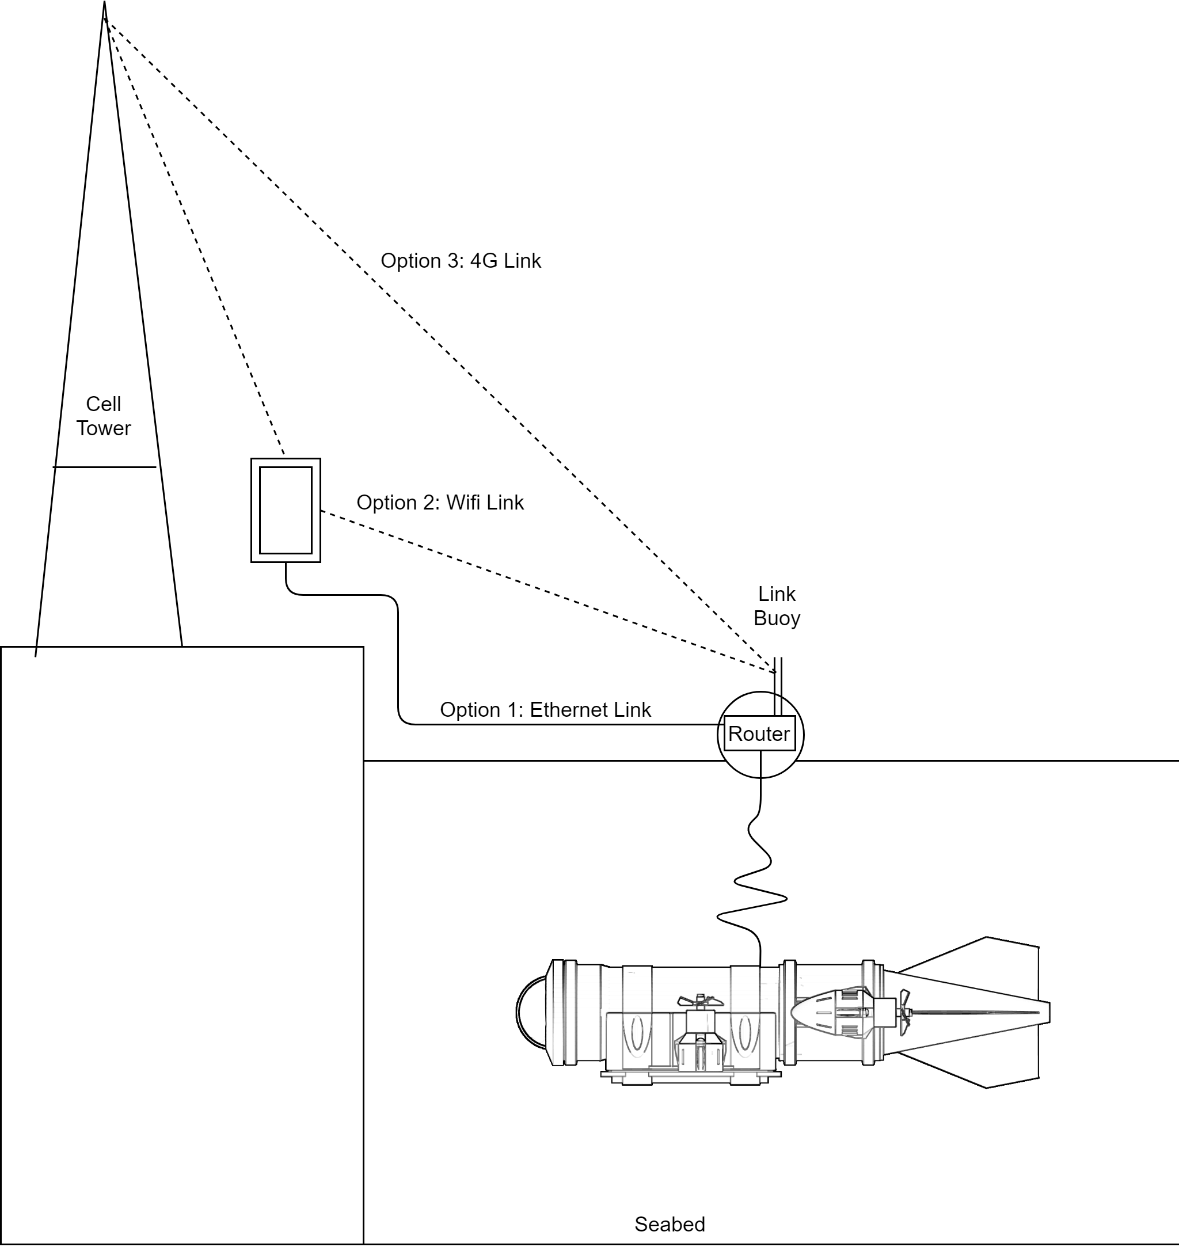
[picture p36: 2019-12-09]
_schematics/Setup.png

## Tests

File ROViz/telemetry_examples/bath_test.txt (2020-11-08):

1569768233864 -2 -4 -3 0.00 0 0 0 0 25.2 787.6 28.2 12.4 
1569768233970 -1 -4 -3 0.00 0 0 0 0 25.2 787.6 28.2 12.4 
1569768234073 -1 -4 -3 0.00 0 0 0 0 25.2 787.6 28.2 12.4 
1569768234178 -1 -4 -3 0.00 0 0 0 0 25.2 787.6 28.2 12.4 
1569768234281 -1 -3 -3 0.00 0 0 0 0 25.2 787.6 28.2 12.4 
1569768234386 -1 -3 -2 0.00 0 0 0 0 25.2 787.6 28.2 12.4 
1569768234489 -1 -3 -2 0.00 0 0 0 0 25.2 787.6 28.2 12.4 
1569768234594 -1 -3 -2 0.00 0 0 0 0 25.2 787.6 28.2 12.4 
1569768234697 -1 -3 -2 0.00 0 0 0 0 25.2 787.6 28.2 12.4 
1569768234802 -1 -3 -2 0.00 0 0 0 0 25.2 787.6 28.2 12.4 
1569768234905 -1 -3 -3 0.00 0 0 0 0 25.2 787.6 28.2 12.4 
1569768235009 0 -3 -3 0.00 0 0 0 0 25.2 787.6 28.2 12.4 
1569768235112 0 -3 -3 0.00 0 0 0 0 25.2 787.6 28.2 12.4 
1569768235217 0 -3 -3 0.00 0 0 0 0 25.2 787.6 28.2 12.4 
1569768235320 0 -3 -3 0.00 0 0 0 0 25.2 787.6 28.2 12.4 
1569768235424 0 -4 -3 0.00 0 0 0 0 25.2 787.6 28.2 12.4 
1569768235527 0 -4 -3 0.00 0 0 0 0 25.2 787.6 28.2 12.4 
1569768235631 0 -4 -3 0.00 0 0 0 0 25.2 787.6 28.2 12.4 
1569768235734 0 -4 -3 0.00 0 0 0 0 25.2 787.6 28.2 12.4 
1569768235837 0 -4 -2 0.00 0 0 0 0 25.2 787.6 28.2 12.4 
1569768235942 0 -4 -2 0.00 0 0 0 0 25.2 787.6 26.1 12.4 
1569768236048 0 -4 -2 0.00 0 0 0 0 25.2 787.6 26.1 12.4 
1569768236152 0 -4 -2 0.00 0 0 0 0 25.2 787.6 26.1 12.3 
1569768236257 0 -4 -3 0.00 0 0 0 0 25.2 787.6 26.1 12.3 
1569768236360 0 -4 -3 0.00 0 0 0 0 25.2 787.6 26.1 12.4 
1569768236464 1 -4 -3 0.00 0 0 0 0 25.2 787.6 26.1 12.4 
1569768236567 1 -4 -3 0.00 0 0 0 0 25.2 787.6 26.1 12.4 
1569768236671 1 -4 -4 0.00 0 0 0 0 25.2 787.6 26.1 12.4 
1569768236775 1 -4 -4 0.00 0 0 0 0 25.2 787.6 26.1 12.4 
1569768236879 1 -4 -4 0.00 0 0 0 0 25.2 787.6 26.1 12.4 
1569768236983 1 -4 -3 0.00 0 0 0 0 25.2 787.6 26.1 12.4 
1569768237102 1 -5 -3 0.00 0 0 0 0 25.2 787.6 26.1 12.4 
1569768237207 1 -5 -3 0.00 0 0 0 0 25.2 787.6 26.1 12.4 
1569768237315 2 -5 -3 0.00 0 0 14 -7 25.2 787.6 26.1 12.4 
1569768237424 2 -5 -2 0.00 0 0 20 -12 25.2 787.6 26.1 12.3 
1569768237533 2 -4 -3 0.00 0 0 25 -19 25.2 787.6 26.1 12.3 
1569768237640 2 -5 -3 0.00 0 0 27 -20 25.2 787.6 26.1 12.1 
1569768237744 2 -5 -3 0.00 0 0 27 -20 25.2 787.6 26.1 12.1 
1569768237852 2 -5 -4 0.00 0 0 0 0 25.2 787.6 26.1 12.1 
1569768237957 3 -4 -4 0.00 0 0 0 0 25.2 787.6 26.1 12.1 
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

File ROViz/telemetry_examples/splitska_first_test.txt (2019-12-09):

1564025840006 32 -11 0 0.00 0 0 0 29.8 36.3 12.9 
1564025840115 32 -11 0 0.00 0 0 0 29.8 36.3 12.9 
1564025840221 32 -11 0 0.00 0 0 0 29.8 36.3 12.9 
1564025840326 33 -11 0 0.00 0 0 0 29.8 36.3 12.9 
1564025840431 32 -11 0 0.00 0 0 0 29.8 36.3 12.9 
1564025840536 33 -5 0 0.00 0 0 0 29.8 36.3 12.9 
1564025840641 32 -11 0 0.00 0 0 0 29.8 36.3 12.9 
1564025840746 32 -11 0 0.00 0 0 0 29.8 36.3 12.9 
1564025840851 32 -11 0 0.00 0 0 0 29.8 36.3 12.9 
1564025840956 32 -11 0 0.00 0 0 0 29.8 36.3 12.9 
1564025841061 32 -11 0 0.00 0 0 0 29.8 36.3 12.9 
1564025841165 32 -11 0 0.00 0 0 0 29.8 36.3 12.9 
1564025841271 32 -11 0 0.00 0 0 0 29.8 36.3 12.9 
1564025841376 33 -11 0 0.00 0 0 0 29.8 36.3 12.9 
1564025841481 32 -11 0 0.00 0 0 0 29.8 36.3 12.9 
1564025841586 32 -11 0 0.00 0 0 0 29.8 36.3 12.9 
1564025841691 32 -11 0 0.00 0 0 0 29.8 36.3 12.9 
1564025841796 32 -11 0 0.00 0 0 0 29.8 36.3 12.9 
1564025841901 32 -11 0 0.00 0 0 0 29.8 36.3 12.9 
1564025842006 32 -11 0 0.00 0 0 0 29.8 36.3 12.9 
1564025842111 32 -11 0 0.00 0 0 0 29.8 36.3 12.9 
1564025842216 32 -11 0 0.00 0 0 0 29.8 36.3 12.9 
1564025842321 32 -11 0 0.00 0 0 0 29.8 36.3 12.9 
1564025842426 32 -11 0 0.00 0 0 0 29.8 36.3 12.9 
1564025842531 32 -11 0 0.00 0 0 0 29.8 36.3 12.9 
1564025842636 32 -11 0 0.00 0 0 0 29.8 36.3 12.9 
1564025842742 32 -11 0 0.00 0 0 0 29.8 36.3 12.9 
1564025842849 32 -11 0 0.00 0 0 0 29.8 36.3 12.9 
1564025842955 32 -11 0 0.00 0 0 0 29.8 36.3 12.9 
1564025843063 32 -11 0 0.00 0 0 0 29.8 36.3 12.9 
1564025843169 32 -11 0 0.00 0 0 0 29.8 36.3 12.9 
1564025843274 32 -11 0 0.00 0 0 0 29.8 36.3 12.9 
1564025843380 32 -11 0 0.00 0 0 0 29.8 36.3 12.9 
1564025843485 32 -11 0 0.00 0 0 0 29.8 36.3 12.9 
1564025843592 32 -11 0 0.00 0 0 0 29.8 36.3 12.9 
1564025843697 32 -11 0 0.00 0 0 0 29.8 36.3 12.9 
1564025843804 32 -11 0 0.00 0 0 0 29.8 36.3 12.9 
1564025843910 32 -11 0 0.00 0 0 0 29.8 36.3 12.9 
1564025844016 32 -11 0 0.00 0 0 0 29.8 36.3 12.9 
1564025844122 32 -11 0 0.00 0 0 0 29.8 36.3 12.9 
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

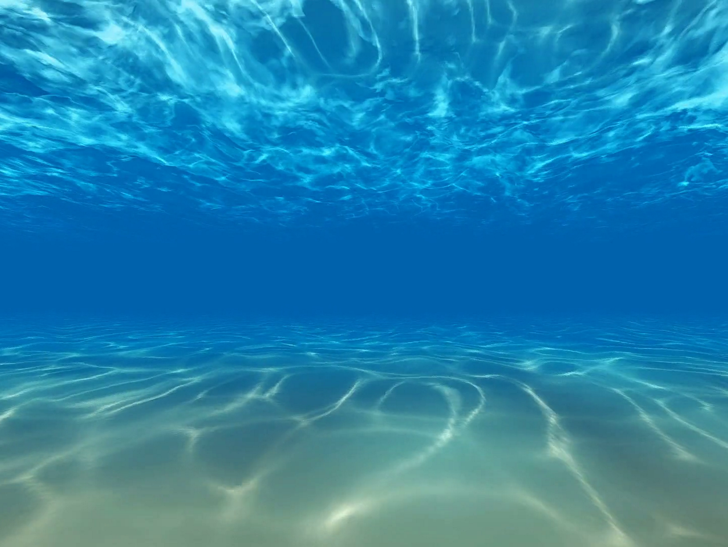
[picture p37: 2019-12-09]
ROVCommander/Assets/Img/testImg.png

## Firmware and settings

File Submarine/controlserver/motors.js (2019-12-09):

var pigpio = require('pigpio');
var Gpio = pigpio.Gpio;

pigpio.configureClock(2, pigpio.CLOCK_PCM);

//https://github.com/fivdi/pigpio/blob/master/doc/gpio.md#pwmrangerange

var left = {
    pwm: new Gpio(17, {mode: Gpio.OUTPUT}),
    dir: new Gpio(18, {mode: Gpio.OUTPUT}),
    name: "left",
    prevSpd: undefined
}

var right = {
    pwm: new Gpio(22, {mode: Gpio.OUTPUT}),
    dir: new Gpio(23, {mode: Gpio.OUTPUT}),
    name: "right",
    prevSpd: undefined
}

var left_depth = {
    pwm: new Gpio(21, {mode: Gpio.OUTPUT}),
    dir: new Gpio(20, {mode: Gpio.OUTPUT}),
    name: "left_depth",
    prevSpd: undefined
}

var right_depth = {
    pwm: new Gpio(26, {mode: Gpio.OUTPUT}),
    dir: new Gpio(19, {mode: Gpio.OUTPUT}),
    name: "right_depth",
    prevSpd: undefined
}

function initMotor(motor){
    console.log("Init motor driver: "+motor.name);

    motor.pwm.pwmFrequency(20000);
    motor.pwm.pwmRange(100);
    motor.pwm.pwmWrite(0);

    motor.dir.digitalWrite(1);
}

function setSpeed(spd, motor){ //0-100 range

	if(motor.prevSpd == spd)
		return;

	motor.prevSpd = spd;

	console.log("SetSpeed:"+Math.round(spd)+", on motor: "+motor.name);
    if(spd < 0)
        motor.dir.digitalWrite(0);
    else if(spd > 0)
        motor.dir.digitalWrite(1);
    motor.pwm.pwmWrite(Math.round(Math.abs(spd)));
}

function clamp(val, mn, mx){
	if(val > mx)
		return mx;
	if(val < mn)
		return mn;
	return val;
}

function setForwardSpeed(left_speed, right_speed){
    setSpeed(left_speed,left);
    setSpeed(right_speed,right);
}

function setDepthSpeed(left_speed, right_speed){
	setSpeed(left_speed,left_depth);
	setSpeed(right_speed,right_depth);
}

function stopAll(){
	setSpeed(0,left_depth);
	setSpeed(0,right_depth);
	setSpeed(0,left);
    setSpeed(0,right);
}


initMotor(left);
initMotor(right);
initMotor(left_depth);
initMotor(right_depth);

module.exports.stopAll = stopAll;
module.exports.setForwardSpeed = setForwardSpeed;
module.exports.setDepthSpeed = setDepthSpeed;

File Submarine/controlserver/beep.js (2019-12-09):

var pigpio = require('pigpio');
var Gpio = pigpio.Gpio;

var speaker = new Gpio(21, {mode: Gpio.OUTPUT});

speaker.pwmFrequency(20000);
speaker.pwmRange(100);
speaker.pwmWrite(0);

function startup(){
	
	speaker.pwmWrite(10);
	
	setTimeout(function()
	{
		speaker.pwmWrite(0);
		setTimeout(function()
		{
			speaker.pwmWrite(15);

			setTimeout(function()
			{
				speaker.pwmWrite(0);
				setTimeout(function()
				{
					speaker.pwmWrite(20);

					setTimeout(function()
					{
						speaker.pwmWrite(0);				
					},120);
				},100);
			},100);
		},100);		
	},10);
}

function single(){
	
	speaker.pwmWrite(15);
	
	setTimeout(function(){
		speaker.pwmWrite(0);
	},200);
}

module.exports.single = single;
module.exports.startup = startup;

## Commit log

2020-11-08 added ROViz
    [Boat.obj, Rock.obj, Seaweed.obj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]
2021-07-30 added cad models
    [actioncam_mount.stl, battery_compartment_front.stl, battery_compartment_rear.stl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]

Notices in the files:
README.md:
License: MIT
